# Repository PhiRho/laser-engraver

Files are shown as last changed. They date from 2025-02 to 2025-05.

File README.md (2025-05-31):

# laser-engraver

I wanted a laser engraver. I also wanted to learn how all the pieces go
together, and how to drive such a thing. This is the collection of 3D objects,
    scripts, CAD designs, etc needed to create one of these things.

## TODO

[x] Complete set of STL and CAD files for driving blocks

[x] Complete set of driving scripts

[x] Instructions for setting up a Pi to use the scripts

[x] Parts list for electro-mechanical components

[x] Full tutorial: [Build a laser
engraver](http://pippah.net/2025/05/31/build-a-laser-engraver/)

### Future Work
- Fix up some of the 3D designs
- Add turtle integration
- Build a UI?
- Dust/smoke extraction

## See also
Check out my blog at [pippah.net](https://pippah.net) to keep up with whatever
I'm thinking about that week.

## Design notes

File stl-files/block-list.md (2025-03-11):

## List of blocks required

* XDriveEnd.stl
* YDriveEnd.stl
* XSlider.stl
* LooseYSlider.stl
* FixedYSlider.stl
* X-Drive-NEMA17.stl
* Y-Drive-NEMA-17.stl
* LaserMountPlate.stl

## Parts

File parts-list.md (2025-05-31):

# A helpful shopping list

| Got it? | Item Type | Quantity |
|---|---|---|
| | [3mm Pulley](https://www.diyelectronics.co.za/store/pulleys/1086-smooth-idler-pulley-3mm-bore-6mm-belt.html) | 12 |
| | [5mm Toothed Pulley](https://www.diyelectronics.co.za/store/pulleys/1089-toothed-idler-pulley-5mm-bore-20-tooth-6mm-gt2-belt-.html) | 2 |
| | [5mm timing pulley](https://www.communica.co.za/products/hkd-gt2-timing-pulley-20t-5mm) | 2 |
| | [End Switch](https://www.diyelectronics.co.za/store/limit-switches-probes/3363-ramps-14-end-switch-module-for-reprap-3d-printers.html) | 4 |
| | [Linear Bearing](https://www.diyelectronics.co.za/store/linear-bearings/1085-linear-bearing-long-lm8luu-8mm-id-15mm-od.html) | 4 |
| | [Laser Module](https://www.diyelectronics.co.za/store/laser-modules/2031-high-power-laser-module-12v-25w-integrated-driver.html) | 1 |
| | [GT2 Timing Belt](https://www.diyelectronics.co.za/store/belts/5708-gt2-timing-belt-6mm-5m-length-pack.html)| 5m (2 x length of steel) |
| | [Steel Shaft](https://www.diyelectronics.co.za/store/linear-shafts/1903-chromed-linear-shafting-diam-8mm-length-1m.html) | 2x65cm, 2x40cm |
| | [Neodymium Magnets](https://www.diyelectronics.co.za/store/magnets/4435-neodymium-n38-magnets-disk-63x3mm.html) | 4 |
| | [Connector Kit](https://www.diyelectronics.co.za/store/prototyping/1840-sil-connector-kit-310pcs.html) | 1 |
| | [Stepper Motor](https://www.diyelectronics.co.za/store/stepper-motors/43-nema-17-stepper-motor-17a-4-kg-cm.html) | 2 |
| | [Power Supply](https://www.diyelectronics.co.za/store/spares/30-power-supply-12v-240w-20a.html) | 1 |
| | [Step Down Buck](https://www.diyelectronics.co.za/store/switch-mode-modules/5399-dc-dc-step-down-buck-module-fixed-5v-output.html) | 2 |
| | [A4988 Stepper Driver](https://www.netram.co.za/motor-drivers/9340-a4988-stepper-motor-driver-with-small-heatsink.html) | 2 |
| | [Pi Pico](https://www.robotics.org.za/image/cache/wp/gj/pi-foundation/PICO-W2/PICO-W2-001-500x500.webp) | 1 |
| | [100 uF capacitor](https://www.communica.co.za/products/100uf-35vr) | 2 |
| | Jumper cables | ?? |
| | Thin wire | ?? |

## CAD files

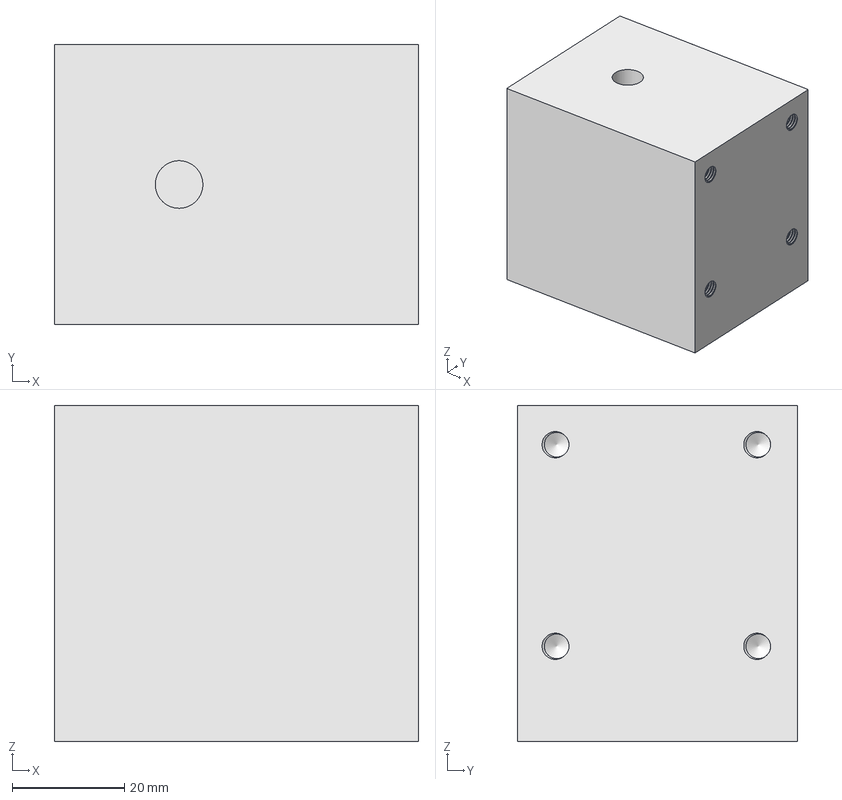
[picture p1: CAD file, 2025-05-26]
cad-files/XDrive-48mmNEMA17.FCStd
65.0 x 50.0 x 60.0 mm

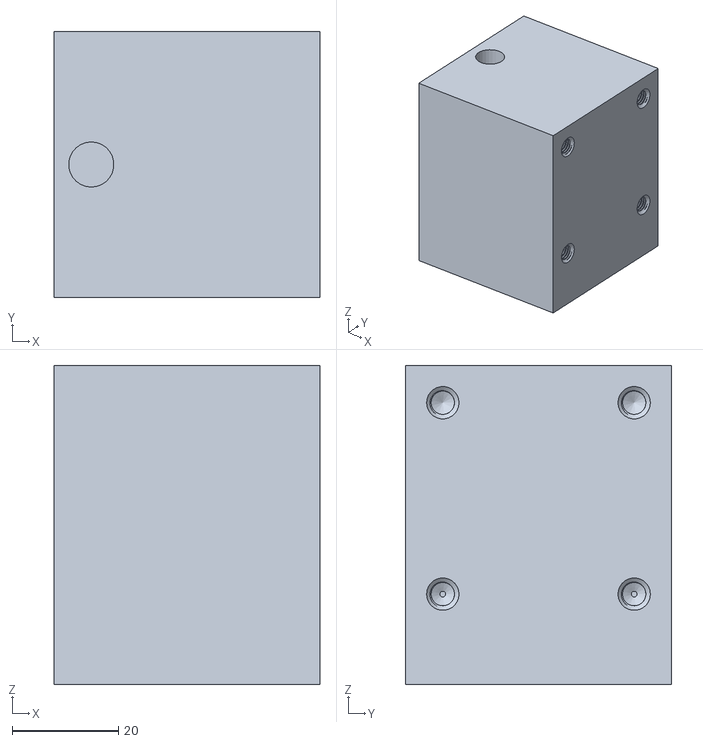
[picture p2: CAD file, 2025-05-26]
stl-files/YDrive-40mmNEMA17-Body.stl
50.0 x 50.0 x 60.0

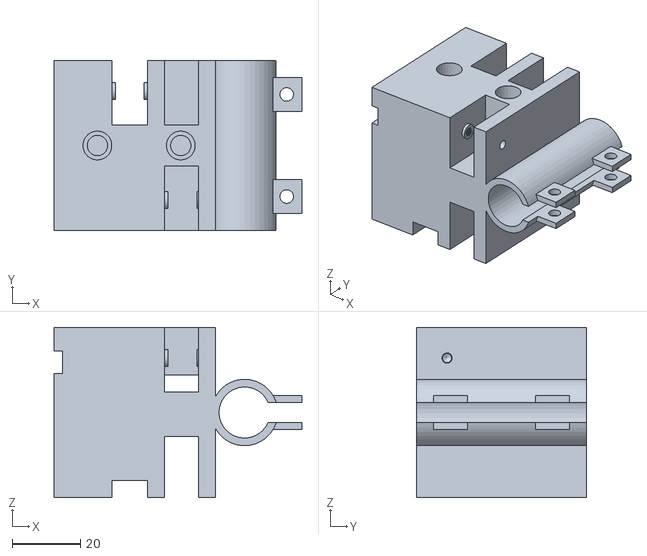
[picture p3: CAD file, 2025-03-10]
stl-files/FixedYSlider.stl
72.9 x 50.0 x 50.0

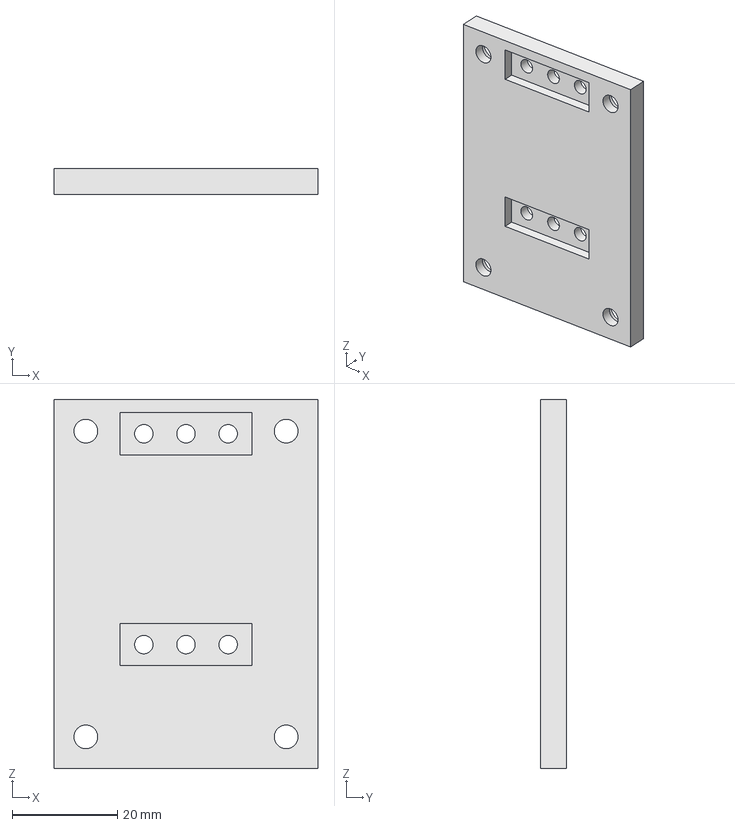
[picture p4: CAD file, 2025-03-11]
cad-files/LaserMountPlate.FCStd
50.0 x 5.00 x 70.0 mm

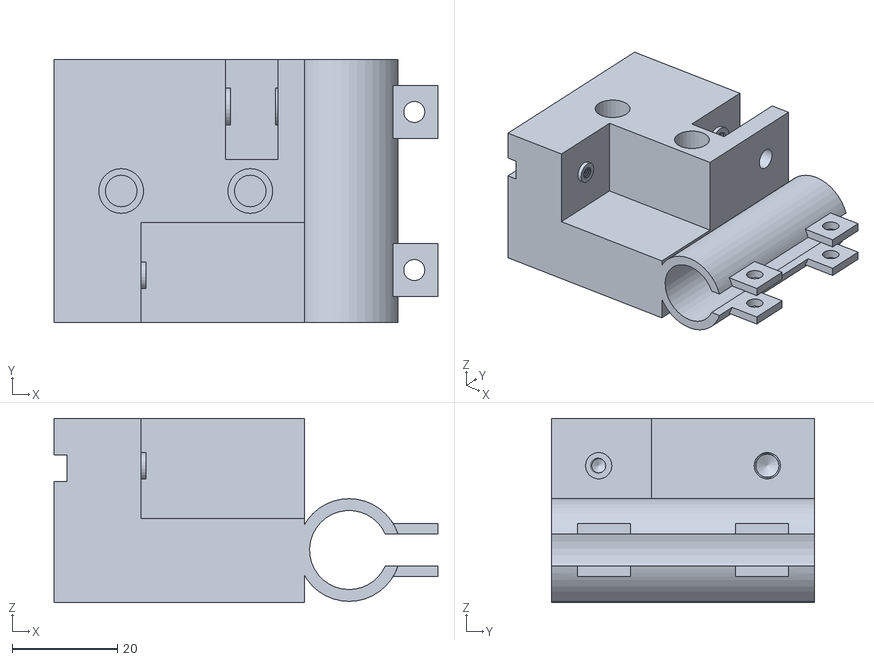
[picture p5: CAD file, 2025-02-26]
stl-files/LooseYSlider.stl
72.9 x 50.0 x 35.0

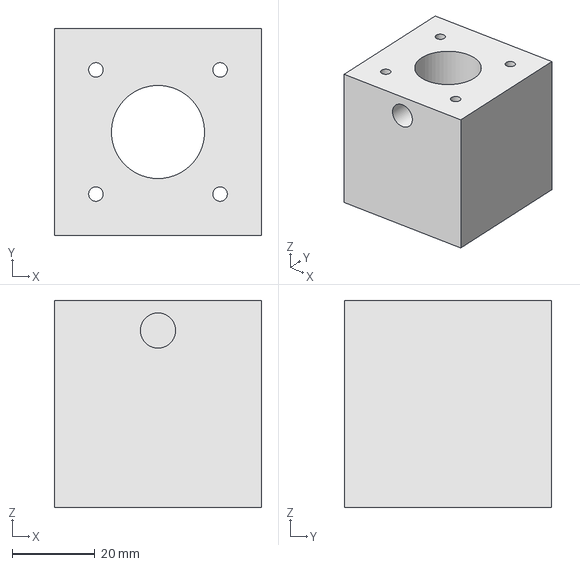
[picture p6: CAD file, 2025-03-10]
cad-files/DrivingCornerBlock.FCStd
50.0 x 50.0 x 50.0 mm

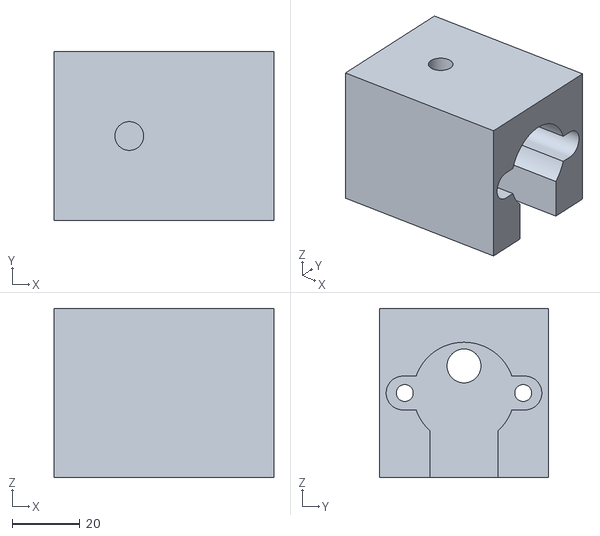
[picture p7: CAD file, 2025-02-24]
stl-files/XDriverBlock.stl
65.0 x 50.0 x 50.0

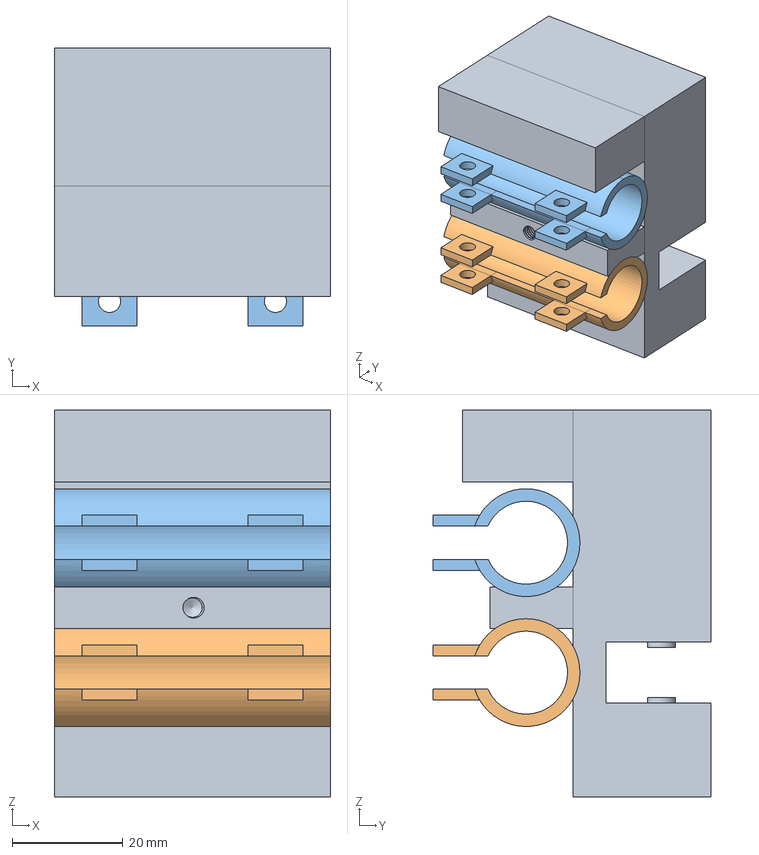
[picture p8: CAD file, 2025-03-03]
cad-files/XSlider.FCStd
50.0 x 50.4 x 70.0 mm

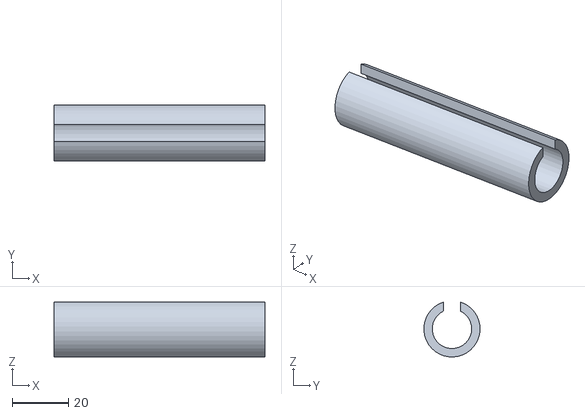
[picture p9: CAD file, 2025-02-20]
stl-files/SandingBlock-rounder.stl
75.0 x 20.0 x 19.5

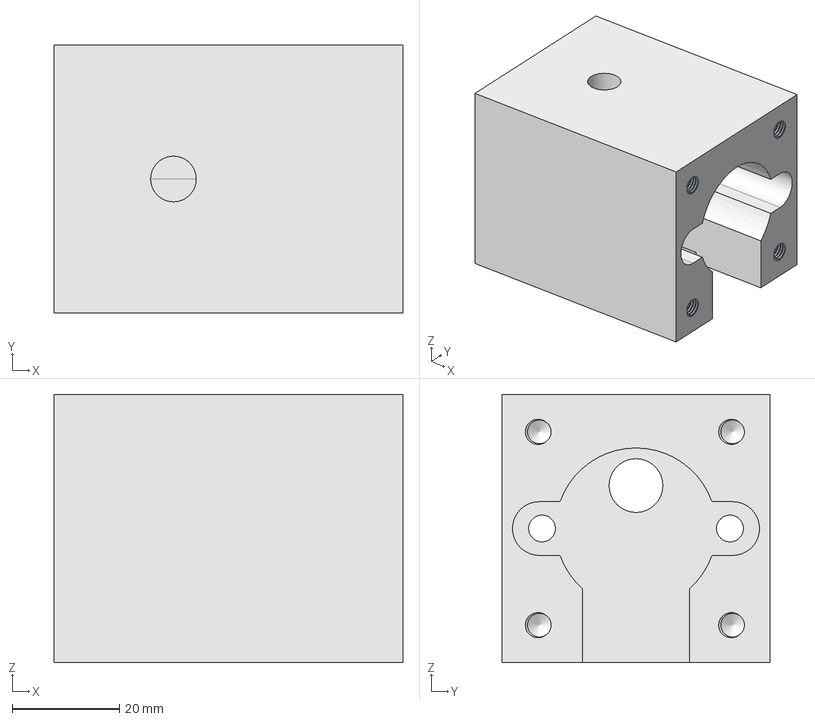
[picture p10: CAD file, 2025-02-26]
cad-files/XDriveCorner.FCStd
65.0 x 50.0 x 50.0 mm

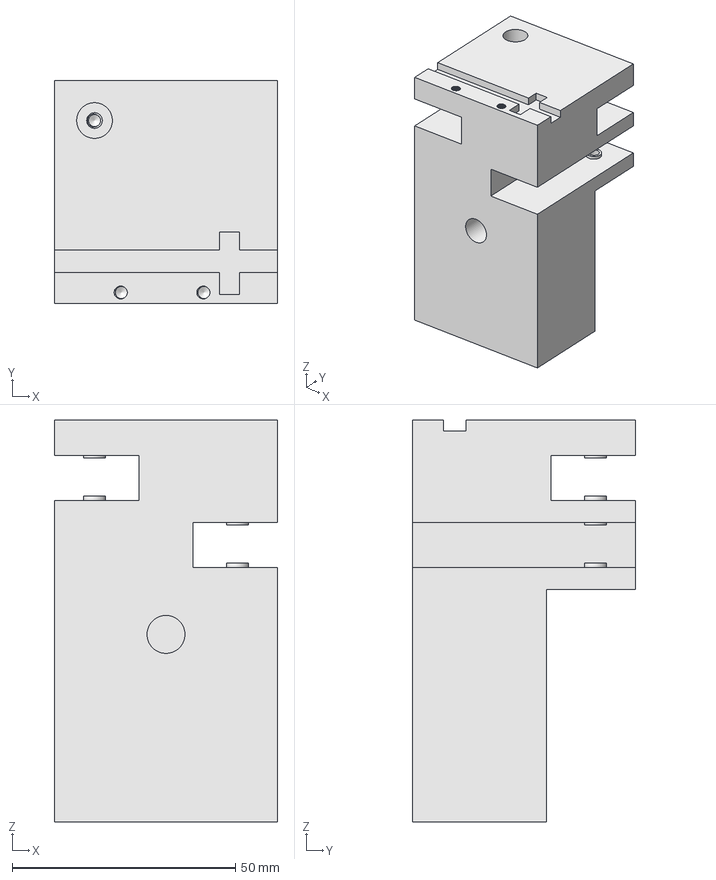
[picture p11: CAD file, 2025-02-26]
cad-files/XDriveEnd.FCStd
50.0 x 50.0 x 90.0 mm

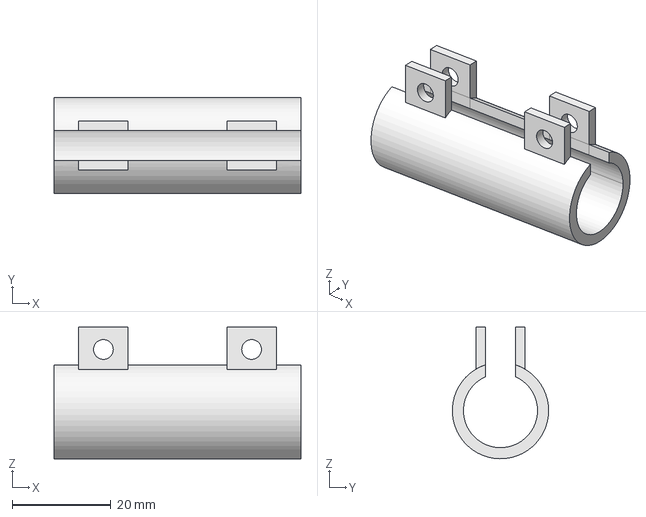
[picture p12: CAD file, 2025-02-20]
cad-files/BearingGrip.FCStd
50.0 x 19.5 x 26.6 mm

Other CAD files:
cad-files/YDrive-40mmNEMA17.FCStd
cad-files/YDriveEnd.FCStd
cad-files/SandingBlock.FCStd
stl-files/LaserMountPlate.stl
stl-files/SandingBlock.stl
stl-files/XDrive-48mmNEMA17.stl
stl-files/XDriveEnd.stl
stl-files/XSlider.stl
stl-files/YDrive-40mmNEMA17.stl
stl-files/YDriveEnd.stl

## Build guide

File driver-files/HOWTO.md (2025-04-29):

## Driving The Engraver

Once all the mechanical parts of the system are put together, you need to be
able to send instructions. This basic collection of files will allow you to do
that. Bearing in mind several factors.

1. Running on a Raspberry PI is not necessarily the _best_ way to put together a
   time sensitive device.
1. This system is intended to be simple and easy to use, but you will have to
   set some numbers - such as the pins you have wired your components to.
1. Some of the libraries used may change under the hood - they are all respected
   OpenSource projects, but if something falls apart then so be it.

### Getting going

The first thing to do, is to set up a virtual python environment to run from. To
do that, if you are _not_ running an ubuntu based system, you can run
```
python3 -m venv /path/to/venv
```

If you _are_ running an ubuntu based system (e.g. doing dev on WSL) you are
going to have to take some extra steps, as the `ensurepip` module is missing.

```
python3 -m venv /path/to/venv --without-pip
wget https://bootstrap.pypa.io/get-pip.py
source /path/to/venv/activate.sh
python get-pip.py
```

Once you have a virtual environment up and running, and have pip installed in
it, you can install dependencies with
```
pip install -r requirements.txt
```

### Running Tests
If you are doing dev work, and want to test functionality, make sure you are in
the `driver-files` folder and run the `pytest` command to run all tests. Full
pytest configuration can be found in `driver-files/pytest.ini`.

### Configuring the pins you've wired
Depending on the accessories you have connected to your device, and the exact device
you are running with, you are going to want to define your own pin numbers for the 
various aspects of the laser. For ease of use, you can define a `.ini` file and provide 
it as an argument to the laser initialisation. Or you can can adjust the `default_pins.ini`
file in your local setup. All sections are required for the engraver to function correctly.

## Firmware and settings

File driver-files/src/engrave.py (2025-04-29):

import logging
from laser_definition import Laser
from motor_definition import Motor
import configparser, os, cmd
from mock_pi import MockPi
import pigpio
import time
from gcode import GCodeInterpreter

logger = logging.getLogger(__name__)

class LaserShell(cmd.Cmd):

    intro = 'Welcome to the laser shell.   Type help or ? to list commands.\n'
    prompt = '(laser) '
    file = None

    def __init__(self):
        super().__init__()
        self.laser = None

    """Do not repeat the previous command (see https://docs.python.org/3/library/cmd.html#cmd.Cmd.emptyline)"""
    def emptyline(self):
        return

    def do_init(self, line):
        'Initialise the Laser device with the specified config file: init default_pins.ini'
        self.laser = initialise_laser(line)

    def do_print(self, line):
        'Print the current config: print'
        print(f"Location is currently {self.laser.location}")
        print(f"Motor X defined as {self.laser.x_motor}")
        print(f"Motor Y defined as {self.laser.y_motor}")
        print(f"X limits defined as {self.laser.x_limits}")
        print(f"Y limit defined as {self.laser.y_limit}")
        print(f"Laser pin defined as {self.laser.laser_pin}")

    def do_draw_to(self, line):
        'Draw a line from the current location to a given location (x,y) with a given speed (mm/s): draw_to 100 100 10'
        try:
            x, y, speed = parse_move_to(line)
            self.laser.laser_on()
            self.laser.move_to(x, y, speed)
            self.laser.laser_off()
        except (ValueError, TypeError) as e:
            print(f"Error executing draw_to command: {e}")
            print("Usage: draw_to <x> <y> <speed>")

    def do_burn(self, line):
        'Turn the laser on for a number of seconds: burn 10'
        try:
            seconds = int(line)
            self.laser.laser_on()
            time.sleep(seconds)
            self.laser.laser_off()
        except (ValueError, TypeError) as e:
            print(f"Error executing burn command: {e}")
            print("Usage: burn <seconds>")


    def do_move_x(self, line):
        'Move the laser a distance (in mm) on the X Axis at speed (in mm/s) and with direction (+/-): move_x 100 10 +'
        try:
            distance, speed, direction = parse_x_movement(line)
            self.laser.move_x(distance, speed, direction)
        except (ValueError, TypeError) as e:
            print(f"Error executing move_x command: {e}")
            print("Usage: move_x <distance> <speed> <direction>")
        except Exception as e:
            print(f"Error executing move_x command: {e}")

    def do_move_y(self, line):
        'Move the laser a distance (in mm) on the Y Axis at speed (in mm/s) and with direction (+/-): move_y 100 10 +'
        try:
            distance, speed, direction = parse_y_movement(line)
            self.laser.move_y(distance, speed, direction)
        except (ValueError, TypeError) as e:
            print(f"Error executing move_y command: {e}")
            print("Usage: move_y <distance> <speed> <direction>")
        except Exception as e:
            print(f"Error executing move_y command: {e}")

    def do_move_to(self, line):
        'Move the laser to a given location (x,y) with a given speed (mm/s): move_to 100 100 10'
        try:
            x, y, speed = parse_move_to(line)
            self.laser.move_to(x, y, speed)
        except (ValueError, TypeError) as e:
            print(f"Error executing move_to command: {e}")
            print("Usage: move_to <x> <y> <speed>")
        except Exception as e:
            print(f"Error executing move_to command: {e}")

    def do_cw_arc(self, line):
        'Move the laser in a clockwise arc ending at a location (x,y) with center point (i,j) and speed (mm/s): cw_arc 100 100 100 100 10'
        try:
            end_x, end_y, center_x, center_y, speed = parse_arc(line)
            self.laser.arc_clockwise(end_x, end_y, center_x, center_y, speed)
        except (ValueError, TypeError) as e:
            print(f"Error executing cw_arc command: {e}")
            print("Usage: cw_arc <end_x> <end_y> <center_x> <center_y> <speed>")
        except Exception as e:
            print(f"Error executing cw_arc command: {e}")

    def do_ccw_arc(self, line):
        'Move the laser in a counterclockwise arc ending at a location (x,y) with center point (i,j) and speed (mm/s): ccw_arc 100 100 100 100 10'
        try:
            end_x, end_y, center_x, center_y, speed = parse_arc(line)
            self.laser.arc_counterclockwise(end_x, end_y, center_x, center_y, speed)
        except (ValueError, TypeError) as e:
            print(f"Error executing ccw_arc command: {e}")
            print("Usage: ccw_arc <end_x> <end_y> <center_x> <center_y> <speed>")
        except Exception as e:
            print(f"Error executing ccw_arc command: {e}")

    def do_draw_file(self, line):
        'Execute a GCode file: draw_file path/to/file.gcode [--dry-run]'
        if not self.laser:
            print("Error: Laser not initialized. Use 'init' command first.")
            return

        try:
            # Parse arguments
            args = line.split()
            if not args:
                print("Usage: draw_file <file_path> [--dry-run]")
                return

            file_path = args[0]
            dry_run = "--dry-run" in args

            # Initialize GCode interpreter with the laser
            interpreter = GCodeInterpreter(self.laser)

            # Read and execute the file
            print(f"Reading GCode file: {file_path}")
            if dry_run:
                print("Performing dry run (no actual movement)")

            instructions = interpreter.read_file(file_path, dry_run=dry_run)

            # Print summary
            print(f"Processed {len(instructions)} instructions")
            if not dry_run:
                print("File execution completed")

        except FileNotFoundError:
            print(f"Error: File not found: {file_path}")
        except ValueError as e:
            print(f"Error: {e}")
        except Exception as e:
            print(f"Error executing GCode file: {e}")

    def do_home(self, line):
        'Set the current location as home (0,0): home'
        self.laser.set_home()

    def do_angle(self, line):
        'Move the laser in a straight line for a given distance, with a given speed, at a given angle (degrees): angle 100 45 10'
        try:
            distance, speed, angle = parse_angle(line)
            self.laser.move_angle(distance, speed, angle)
        except (ValueError, TypeError) as e:
            print(f"Error executing angle command: {e}")
            print("Usage: angle <distance> <speed> <angle>")
        except Exception as e:
            print(f"Error executing angle command: {e}")

    def do_quit(self, line):
        'Quit the engraver: quit'
        if self.laser is not None:
            self.laser.pi.stop()
        return True

def parse_angle(line):
    distance, speed, angle = line.split()
    return int(distance), int(speed), int(angle)

def parse_move_to(line):
    x, y, speed = line.split()
    return float(x), float(y), float(speed)

def parse_x_movement(line):
    distance, speed, direction = line.split()
    if direction == "+":
        direction = True
    else:
        direction = False
    return int(distance), int(speed), direction

def parse_y_movement(line):
    distance, speed, direction = line.split()
    if direction == "-":
        direction = False
    else:
        direction = True
    return int(distance), int(speed), direction

def parse_arc(line):
    end_x, end_y, center_x, center_y, speed = line.split()
    return float(end_x), float(end_y), float(center_x), float(center_y), float(speed)

def main():
    logging.basicConfig(level=logging.DEBUG)
    logger.info("Starting engraver")
    LaserShell().cmdloop()
    logger.info("Engraver finished")

def initialise_laser(config_file):
    if not os.path.exists(config_file):
        logger.error(f"Config file {config_file} not found")
        return None
    config = configparser.ConfigParser()
    config.read(config_file)
    logger.info(f"Found sections {config.sections()}")

    if config.has_section('pi'):
        logger.info("Config has optional pi section")
        pi = MockPi()
    else:
        pi = pigpio.pi()
        if not pi.connected:
            logger.error("Failed to connect to pigpio; did you start the daemon?")
            return None

    x_motor_pins = config['xmotor']
    x_motor = Motor(int(x_motor_pins['step']), int(x_motor_pins['direction']), int(x_motor_pins['ms1']), int(x_motor_pins['ms2']), int(x_motor_pins['ms3']), pi)

    y_motor_pins = config['ymotor']
    y_motor = Motor(int(y_motor_pins['step']), int(y_motor_pins['direction']), int(y_motor_pins['ms1']), int(y_motor_pins['ms2']), int(y_motor_pins['ms3']), pi)

    limit_pins = config['limits']
    x_limits = (int(limit_pins['x_one']), int(limit_pins['x_two']))
    y_limit = int(limit_pins['y_one'])

    laser_pin = int(config['laser']['enable'])

    return Laser(x_motor, y_motor, x_limits, y_limit, laser_pin, pi)



if __name__ == "__main__":
    main()

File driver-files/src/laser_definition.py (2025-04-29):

import logging
import math
import pigpio
import time
import numpy as np
from motor_definition import Motor

class Laser:
    logger = logging.getLogger(__name__)
    """
    A class to control a laser cutter's motors and laser module. This assumes NEMA 17 stepper motors.

    Attributes:
        x_motor: Motor which moves the laser cutter in the x direction
        y_motor: Motor which moves the laser cutter in the y direction
        x_limits: Tuple of GPIO pins for movement limits
        y_limit: Pin number for end limit
        laser_pin: GPIO pin number for controlling the laser module
    """
    def __init__(self, x_motor, y_motor, x_limits, y_limit, laser_pin, pi):
        self.x_motor = x_motor
        self.y_motor = y_motor
        self.x_limits = x_limits
        self.y_limit = y_limit
        self.laser_pin = laser_pin
        self.pi = pi
        self.setup_pins()
        self.location = (0, 0)
        self.stop_motor = False

    def setup_pins(self):
        self.pi.set_mode(self.x_limits[0], pigpio.INPUT)
        self.pi.set_pull_up_down(self.x_limits[0], pigpio.PUD_UP)
        self.pi.set_mode(self.x_limits[1], pigpio.INPUT)
        self.pi.set_pull_up_down(self.x_limits[1], pigpio.PUD_UP)
        self.pi.set_mode(self.y_limit, pigpio.INPUT)
        self.pi.set_pull_up_down(self.y_limit, pigpio.PUD_UP)

        self.pi.set_mode(self.laser_pin, pigpio.OUTPUT)
        self.pi.write(self.laser_pin, 0)

        self.pi.callback(self.x_limits[0], pigpio.FALLING_EDGE, self.interrupt_movement)
        self.pi.callback(self.x_limits[1], pigpio.FALLING_EDGE, self.interrupt_movement)
        self.pi.callback(self.y_limit, pigpio.FALLING_EDGE, self.interrupt_movement)

    def set_home(self):
        self.location = (0, 0)

    def laser_on(self):
        self.pi.write(self.laser_pin, 1)

    def laser_off(self):
        self.pi.write(self.laser_pin, 0)

    """
    Called by `pigpio` when one of the limit switches is depressed. Required to ensure that the
    motors cannot overshoot their bounds.
    """
    def interrupt_movement(self, gpio, level, tick):
        self.laser_off()
        self.stop_motor = True
        time.sleep(0.01)
        self.logger.info(f"GPIO {gpio} has changed state with level {level}")
        if gpio == self.x_limits[0]:
            self.logger.info("X limit 0 hit")
            self.move_x(10, 100, False)
        elif gpio == self.x_limits[1]:
            self.logger.info("X limit 1 hit")
            self.move_x(10, 100, True)
        elif gpio == self.y_limit:
            self.logger.info("Y limit hit")
            self.move_y(10, 100, True)
        self.logger.info(f"Motor move back 10mm")
        self.stop_motor = True

    """Move in a straight line along the X Axis"""
    def move_x(self, distance, speed, positive=True):
        step_count = self.step_count_from_distance(distance)
        step_delay = self.step_delay_from_speed(speed)
        if positive:
            step_size = Motor.MM_PER_STEP
        else:
            step_size = -Motor.MM_PER_STEP
        self.stop_motor = False
        for i in range(step_count):
            if self.stop_motor:
                self.logger.warn("Motor interrupted by limit")
                break
            self.step_x(step_delay, positive)
            self.location = (self.location[0] + step_size, self.location[1])

    def step_x(self, delay, direction):
        if direction:
            self.x_motor.set_direction(Motor.Direction.CLOCKWISE)
        else:
            self.x_motor.set_direction(Motor.Direction.COUNTERCLOCKWISE)
        self.x_motor.step_with_delay(delay)

    """
    Move in a stright line on the Y Axis
    As long as the delay is small enough, the line will be straight.
    But since the motors are not being triggered in parallel this is an approximation at best.
    """
    def move_y(self, distance, speed, positive=True):
        self.y_motor.set_microstep(1)
        step_count = self.step_count_from_distance(distance)
        step_delay = self.step_delay_from_speed(speed)
        if positive:
            step_size = Motor.MM_PER_STEP
        else:
            step_size = -Motor.MM_PER_STEP
        self.stop_motor = False
        for i in range(step_count):
            if self.stop_motor:
                self.logger.warn("Motor interrupted by limit")
                break
            if self.location[1] + step_size > 650:
                self.logger.warn("Reached limit enforced by software on Y-Axis")
                break
            self.step_y(step_delay, positive)
            self.location = (self.location[0], self.location[1] + step_size)

    def step_y(self, delay, direction):
        if direction:
            self.x_motor.set_direction(Motor.Direction.CLOCKWISE)
            self.y_motor.set_direction(Motor.Direction.CLOCKWISE)
        else:
            self.x_motor.set_direction(Motor.Direction.COUNTERCLOCKWISE)
            self.y_motor.set_direction(Motor.Direction.COUNTERCLOCKWISE)
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

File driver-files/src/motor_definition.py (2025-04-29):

import logging
import pigpio
import time
from enum import Enum

class Motor:
    LOGGER = logging.getLogger(__name__)

    MICROSTEP_MATRIX = {
        1: (0, 0, 0),
        2: (1, 0, 0),
        4: (0, 1, 0),
        8: (1, 1, 0),
        16: (1, 1, 1)
    }

    Direction = Enum("Direction", [("CLOCKWISE", 0), ("COUNTERCLOCKWISE", 1)])

    STEPS_PER_REVOLUTION = 200
    TEETH_PER_REVOLUTION = 20
    TOOTH_PITCH = 2 # mm
    MM_PER_STEP = (TOOTH_PITCH * TEETH_PER_REVOLUTION) / STEPS_PER_REVOLUTION

    """
    A class to control a stepper motor. This assumes an A4988 stepper motor driver.

    Attributes:
        step: GPIO pin number for the step signal
        direction: GPIO pin number for the direction signal
        ms1: GPIO pin number for the ms1 signal
        ms2: GPIO pin number for the ms2 signal
        ms3: GPIO pin number for the ms3 signal
    """
    def __init__(self, step, direction, ms1, ms2, ms3, pi):
        self.step = step
        self.direction = direction
        self.ms1 = ms1
        self.ms2 = ms2
        self.ms3 = ms3
        self.pi = pi
        self.enable_pins()
        self.LOGGER.info("Motor initialized with pins: Step: %s, Direction: %s, MS1: %s, MS2: %s, MS3: %s", self.step, self.direction, self.ms1, self.ms2, self.ms3)
        self.set_microstep(1)

    def enable_pins(self):
        self.pi.set_mode(self.step, pigpio.OUTPUT)
        self.pi.set_mode(self.direction, pigpio.OUTPUT)
        self.pi.set_mode(self.ms1, pigpio.OUTPUT)
        self.pi.set_mode(self.ms2, pigpio.OUTPUT)
        self.pi.set_mode(self.ms3, pigpio.OUTPUT)

    def set_microstep(self, microstep):
        self.pi.write(self.ms1, self.MICROSTEP_MATRIX[microstep][0])
        self.pi.write(self.ms2, self.MICROSTEP_MATRIX[microstep][1])
        self.pi.write(self.ms3, self.MICROSTEP_MATRIX[microstep][2])
        self.LOGGER.debug("Microstep set to: %s", microstep)

    def set_direction(self, direction):
        self.pi.write(self.direction, direction.value)

    def step_with_delay(self, delay):
        self.pi.write(self.step, 1)
        time.sleep(delay)
        self.pi.write(self.step, 0)

    def __str__(self):
        direction_state = self.pi.read(self.direction)
        direction = "COUNTERCLOCKWISE" if direction_state == 1 else "CLOCKWISE"
        return f"Motor(step={self.step}, direction={self.direction}[{direction}], ms1={self.ms1}, ms2={self.ms2}, ms3={self.ms3})"

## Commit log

2025-02-20 Add an initial set of driving blocks
    [50mmLooseDrivingCorner.stl, DrivingCornerBlock-BigWing.stl, DrivingCornerBlock-Body.stl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]
2025-02-20 Add FreeCAD files used to create the driving blocks
    [BearingGrip.FCStd, DrivingCornerBlock.FCStd, SandingBlock.FCStd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]
2025-02-21 Add Y-Drive Side end corner block
    Also fix hole locations for laser connection points and add git
    ignore.
    [50mmLooseDrivingCorner.stl, DrivingCornerBlock.FCStd, XSlider.FCStd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]
2025-02-24 Add X-Drive End block in initial state
    [XDriveEnd.FCStd, XDriveEnd.stl, XSlider.FCStd]
2025-02-24 Update X-Drive End for better geometry
    This change sets the lower pulley at the back of the block to match the
    pulley in the Y-Drive End so that the band runs directly between the
    two.
    [XDriveEnd.FCStd, XDriveEnd.stl, YDriveEnd.FCStd]
2025-02-24 Add X-Driver corner and list of which STL files to print
    The list is for my own use for now, I have these floating files which
    are poorly named and need organising. The list helps with that.
    [XDriveCorner.FCStd, XDriverBlock.stl]
2025-02-24 Pad x-slider to hit limit
    The sliding block must be wide enough at the top to hit the limit switch
    button on each edge regardless of the position of the switch.
    [XSlider.FCStd, XSlider.stl]
2025-02-26 Allow more connecting space and add indents for magnets
    Deeper channels allows better clamping for the timer band, and the
    magnet indents will allow the device to be taken apart for storage or
    travel. The block list is also updated with the latest correct names of
    the STL files.
    [FixedYSlider.stl, LooseYSlider.stl, XSlider.FCStd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]
2025-02-26 Add fixing holes to bases
    These holes will allow the blocks to be screwed to a solid surface,
    ensuring no wobble when the device is in motion.
    [XDriveEnd.FCStd]
2025-02-26 Add mount point for motor driver board
    The motor is connected via a board with a ULN2003 chip, this should be
    mounted to the drive block. This change adds screw holes and a recess
    for the plate to be attached to the driving block, as well as adding
    base mounting holes to stabilise the driving blocks.
    [DrivingCornerBlock.FCStd, XDriveCorner.FCStd, YDriverBlock.stl]
2025-03-03 Redesign of the X-slider with a separate mount plate
    The previous version proved all wrong once the pieces were put together.
    This new design is intended to allow for better access to screws, and to
    allow the laser to be entirely separate from the slider.
    [LaserMountPlate.FCStd, LaserMountPlate.stl, XSlider.FCStd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]
2025-03-10 Add NEMA-17 driver block and fix Y-slider
    [DrivingCornerBlock.FCStd, FixedYSlider.stl, XDrive-48mmNEMA17-Body.stl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]
2025-03-11 Add NEMA-17 Y-Drive block
    This block requires a motor less than 48mm in height in order to allow
    the attachment points to be unchanged. The system has no requirement for
    a larger motor, the only constraint will be availability.
    [YDrive-40mmNEMA17.FCStd, YDrive-40mmNEMA17.stl]
2025-03-11 Cleanup STL files to reduce size and confusion
    This reduces the number of 3D files being stored, and makes all of them
    "required" for the project. Deleting the blocks which have been
    refactored along the way.
    [50mmLooseDrivingCorner.stl, DrivingCornerBlock-BigWing.stl, DrivingCornerBlock-Body.stl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]
2025-03-11 Fix hole layout for laser mount
    [LaserMountPlate.FCStd, LaserMountPlate.stl]
2025-03-13 Fix rail position in Y Drive
    [YDrive-40mmNEMA17.FCStd, YDrive-40mmNEMA17.stl]
2025-03-13 Create a basic driver script
    This doesn't have much in the way of complexity, and is intended
    to verify that the motors are working and wired correctly.
    GPIO docs:
    https://sourceforge.net/p/raspberry-gpio-python/wiki/browse_pages/
    Script originated at
    https://tutorials-raspberrypi.com/how-to-control-a-stepper-motor-with-raspberry-pi-and-l293d-uln2003a/
2025-03-13 Add a laser management class with stub tests
    Using cursor to generate some of the boiler plate. Tests will be updated
    to actually verify movement works as anticipated. These classes will
    form the base of the proper GCode reading for the project.
2025-03-13 Begin testing basic Motor functions
    This introduces a dumb mock for the pi daemon from pigpio since starting
    a daemon to run these tests isn't useful.
2025-03-13 Pull out a couple of the functions for testability
    Tests highlight misunderstandings, particularly around functions like
    `sleep` which take an argument in seconds not milliseconds.
2025-03-13 Add pin storage to MockPi
    By keeping track of pin assignments and values in the mock, the basic
    functionality becomes easier to verify.
2025-03-13 Further refactoring to simplify parallel motor commands
2025-03-13 Begin the process of making this runnable
    Setting a config file for the pin definitions and creating a landing
    place for running from. Also modifying HOWTO to include mention of
    config.
2025-03-14 Rearrange the world such that command line works
    The laser shell uses the MockPi object if the section in in the config,
    which allows it to be run on a device which is not running the
    `pigiod` process.
2025-03-14 Update motor pins to match reality
2025-03-14 Don't re-assign pin as INPUT
    Also some utility updates
2025-03-15 Print more details and troubleshoot limits
2025-03-15 Cleanup strings, fix tests, add more limit debugging
    [engrave.py, laser_definition.py]
2025-03-18 Add stright line angle and fix printing issue
    [engrave.py, laser_definition.py, motor_definition.py]
2025-04-08 flip x-zero side and fix move_angle bug
    [laser_definition.py]
2025-04-08 Flip triangles in negative quadrants
    [laser_definition.py]
2025-04-08 Make arc steps bigger and add error handling to input
    [engrave.py, laser_definition.py]
2025-04-10 Pull the trigger and turn on the laser
    This finally adds the software switch on the laser. Making it possible
    to test final functionality.
2025-04-10 Add a testing burn command
    [engrave.py]
2025-04-21 Add GCodeInterpreter class to process GCode files
    This commit introduces the GCodeInterpreter class, which reads and interprets GCode files, handling commands for laser operations, movement, and unit settings. It includes methods for reading files, processing individual lines, and executing commands with error handling and logging. The class supports both dry runs and actual execution with a connected laser.
    [gcode.py]
2025-04-21 Add GCode file execution capability to LaserShell
    This commit introduces the 'draw_file' command in the LaserShell class, allowing users to execute GCode files. It includes error handling for file operations and supports a dry run mode to simulate execution without actual movement. The GCodeInterpreter is utilized to read and process the GCode instructions, enhancing the functionality of the laser control interface.
    [engrave.py]
2025-04-21 Update GCodeInterpreter to use a lower speed of 200 mm/s for G0 movements
2025-04-21 Add laser pin initialization in Laser class
    This commit sets the laser pin as an output and initializes it to low, ensuring the laser is properly configured for operation.
2025-05-26 Latest revision of 3D parts
    [XDrive-48mmNEMA17.FCStd, XDrive-48mmNEMA17.stl, YDrive-40mmNEMA17-Body.stl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]
